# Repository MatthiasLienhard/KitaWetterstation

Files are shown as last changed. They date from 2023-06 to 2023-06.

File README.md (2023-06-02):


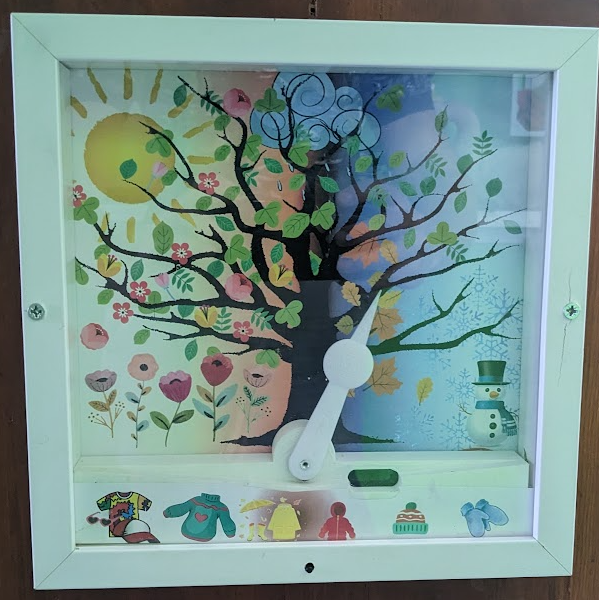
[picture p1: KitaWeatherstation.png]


# KitaWetterstation
Weather station with animations for kindergarden.
This video shows the weather station in action: https://youtu.be/sKCQWrAyeEQ
The 3d model files are also on thingiverse: https://www.thingiverse.com/thing:6057646

# Function
A press on the button wakes the ESP32 from deep sleep. It connects to wifi, and displays an animation with the LEDs and pointer. After wifi is established, the DWD weather API is queried for the current local weather information. This information is evaluated into 5 categories, mainly on temperature and rainfall. The category is displayed with the pointer, and corresponding clothing lights up. The OLED display also shows the weather information with an icon, and the exact temperature. Further it used to display battery state and issues, such as problems with the wifi connection. 
The device is battery operated. The battery is expected to run about 1 week before it needs recharging with a USB charger. 

# Implementation
The project is implemented in micropython, with asyncio to facilitate processing of concurrent tasks. For the first use, I implemented a function save_wifi(ssid, pw) to setup a wifi connection to an access point. This creates a file credentials.txt storing this information. 

# Components
* Ikea Frame SANNAHED 25x25 cm
* 3d printed base to hold the motor and hide the electronics in the frame. 
* Artwork for the background and the clothing items to light up. 
* ESP32 dev board with battery charging circuit and low standby current. I used TTGO T7
* SG90 Hobby servo motor.
* 6 LEDs of a RGB Neopixel stripe 
* I2C oled display 0.92'', 128X32 pixel.
* 1000 mAh lithium ion battery 
* tactile button
* some mosfets to reduce standby current of LEDs and Motor. I used IRLML6344 and SI2305 for a high side switch. Since these are SOT-23 SMD components I used adapter PCBs to integrate them in the circuit.

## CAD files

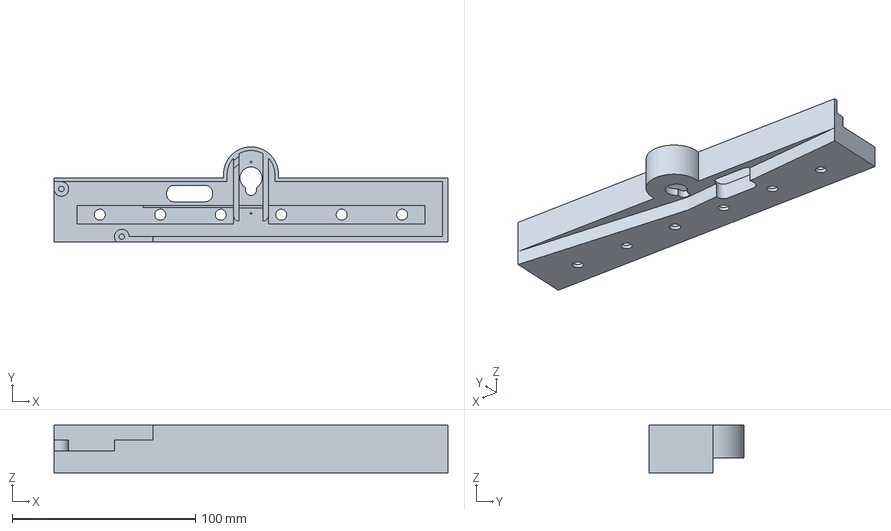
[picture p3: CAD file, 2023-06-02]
3dmodel/kitathermometer-Body.3mf
215.0 x 52.0 x 26.0 mm

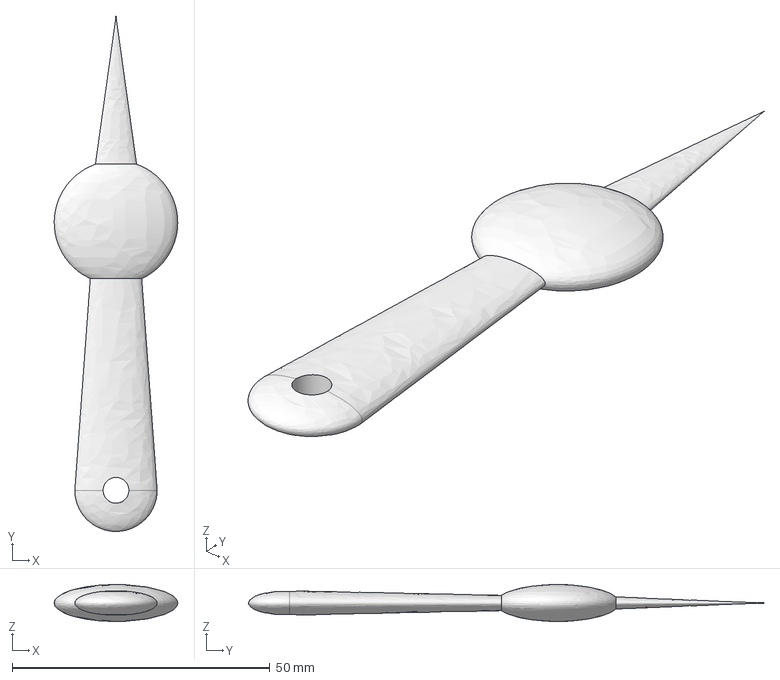
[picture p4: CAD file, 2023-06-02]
3dmodel/zeiger.FCStd
24.0 x 100.0 x 7.19 mm

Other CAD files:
3dmodel/kitathermometer.FCStd
3dmodel/kitathermometer.3mf
3dmodel/zeiger.3mf

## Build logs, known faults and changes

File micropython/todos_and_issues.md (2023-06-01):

todo: webrequest assync
zones:>30: sonnenchreme, <30 t-shirt, <20 pulli, rain: regenjacke, <15: jacke,  <10: Mütze,  <5: Handschuhe

priority: 2<1<3<4<5<6<7
save zone thresholds

save last weather result
only request if d time > 15 minutes

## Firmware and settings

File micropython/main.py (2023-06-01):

# main.py -- put your code here!
from servo import Servo
from display import Display
import neopixel
import time
from machine import deepsleep, Pin, I2C, ADC
import esp32
import utils
from utils import save_wifi as wifi
from utils import save_thresholds

from bitmap import BitMap
import uasyncio as asyncio

# initialization
wakeup_pin = Pin(4, Pin.IN, pull=Pin.PULL_UP,value=1, hold=True)

power_pin = Pin(33, Pin.OUT, value=1)  # activate VBAT
battery_pin = ADC(Pin(35), atten=ADC.ATTN_11DB)
vbat = battery_pin.read_uv()/1000000*2
print('battery voltage: {}V'.format(vbat))
i2c = I2C(0, scl=Pin(22), sda=Pin(21))
display = Display(i2c, 128, 40, False, start_msg=None)
# battery between 3.5 (empty) and 4V (full)
display.battery(80, 10, charge=max(0, min(100, (vbat-3.5)/.5*100)))
display.text('{:.1f}V'.format(vbat),80, 24)
if vbat < 3.5:
    display.show()
    power_pin.value(0)  # VBat inactive
    
    esp32.wake_on_ext0(pin = wakeup_pin, level = esp32.WAKEUP_ALL_LOW)
    time.sleep(3)
    display.poweroff()
    deepsleep()


np = neopixel.NeoPixel(Pin(17), 6)
servo = Servo(pin=Pin(16), pwm_freq=50, min_ms=.4,
              max_ms=2.15, range_degrees=90)


# shutdown 
def shutdown():
    for i in range(len(np)):
        np[i] = 0, 0, 0
    np.write()
    servo.pwm.deinit()
    print('go to sleep...')
    power_pin.value(0)  # inactive
    # _ = wakeup_pin.irq(handler=None, trigger=Pin.IRQ_FALLING,
    #                   wake=DEEPSLEEP)  # configure wakeup
    esp32.wake_on_ext0(pin = wakeup_pin, level = esp32.WAKEUP_ALL_LOW)
    display.poweroff()
    
    deepsleep()
icon_names = [['cloud', 'rainbow', 'snow', 'clear-day'], ['cloudy', 'rain', 'cloudy-wind', 'wind'],
              ['partly-cloudy-day', 'clear-night', 'sleet', 'degree'], ['unknown', 'wifi', 'None', 'None']]
icons_all = BitMap.from_file('weather-icon-set.bmp')
icons = {}

for i in range(4):
    for j in range(4):
        if icon_names[i][j] != 'None':
            icons[icon_names[i][j]] = icons_all.crop(30*j, 30*i, 30, 30)

icons['partly-cloudy-night'] = icons['partly-cloudy-day']
icons['fog'] = icons['cloud']
icons['hail'] = icons['snow']
icons['thunderstorm'] = icons['rain']

numbers_all = BitMap.from_file('numbers.bmp')
numbers = {}
for i in range(10):
    numbers[str(i)] = numbers_all.crop(20*i, 0, 20, 30)
numbers[','] = numbers_all.crop(200, 0, 10, 30)
numbers['.'] = numbers_all.crop(210, 0, 10, 30)
numbers['-'] = numbers_all.crop(220, 0, 15, 30)
del numbers_all


del icons_all
# del icon_names
gc.collect()

# missing icons


display.draw_image(icons['wifi'], 40, 2, invert=True)
display.show()


async def main():
    display_task = asyncio.create_task(display.cycle_images(
        [None, icons['wifi']], 40, 2, invert=True, delay=.2))
    neopixel_task = asyncio.create_task(utils.np_animation(
        np, fun=utils.colorband, steps=30, np_diff=.05, brightness=30))
    # neopixel_task=asyncio.create_task(utils.np_animation(np, fun= utils.kitt,steps=20, back=True, brightness=10))
    servo_task=asyncio.create_task(servo.steps(positions=[0, 1/3, 2/3, 1, 2/3, 1/3, 0,-1/3, -2/3,-1, -2/3, -1/3 ],  sleeptime=1/6))
    connected = False
    connected = await utils.connect_wlan(*utils.read_credentials())
    #await asyncio.sleep(10)
    
    display_task.cancel()
    display.draw_image(icons['wifi'], 40, 2, invert=True)
    if not connected:
        for shift in range(3):
            display.line(39+shift, 2, 69+shift, 32, 1)
            display.line(39+shift, 32, 69+shift, 2, 1)
            display.show()
            
    else:
        #todo: depend on machine.reset_cause() 
        
        #display.fill_rect(0,0,128,32,False)
        display.fill(0)
        display.draw_image( icons['unknown'], 0,2, True)
        display.draw_image( icons['unknown'], 45,2, True)
        display.draw_image( icons['unknown'], 90,2, True)
        #display.text('Messstation',32,24)
        display.show()
        

        wetter = utils.get_weather()
        if wetter['temperature'] is None:
            utils.set_local_time()
            display.fill_rect(0,24,128,8,False)
            display.text('Vorhersage',32,24)
            display.show()
            wetter = utils.get_weather_fc()

        for k, v in wetter.items():
            print('{}: {}'.format(k, v))

        display.fill(0)
        # display.text(['{} and {}'.format(wetter['condition'], wetter['icon']),'{}*C'.format(wetter['temperature'])], valign=1, halign=1)
        # display.draw_image(icons.get(str(wetter.get('icon')), icons['unknown']), 0,2,True)
        print('draw icon')
        display.draw_image(icons.get(str(wetter.get('icon')), icons['unknown']), 0, 0, True)
        offset = 30
        if wetter.get('temperature') is None:
            display.draw_image(icons['unknown'], offset, 2, True)
        else:
            for c in str(wetter['temperature']):
                digit = numbers[c]
                display.draw_image(digit, offset, 2, True)
                offset += digit.width
            display.draw_image(icons['degree'], offset, 2, True)
        rain=wetter.get('precipitation_10', wetter.get('precipitation'))
        if rain:
            msg='{}mm'.format(rain)
            display.fill_rect(0,24,8*len(msg),8,False)
            display.text(msg,0,25)
        display.show()

        temp_range = (5, 25)
        if wetter.get('temperature') is not None and rain is not None:
            servo_task.cancel()
            neopixel_task.cancel()

            zone, lights=utils.get_zone(wetter['temperature'], rain)
            color=utils.heatcolor(wetter['temperature']/30, 50)
            for i in range(6):
                if i in lights:
                    np[i]=color
                else:
                    np[i]=0,0,0
            np.write()
            # servo_pos = ((wetter['temperature']-temp_range[0]) /
            #            (temp_range[1]-temp_range[0])-.5)*2
            servo_pos=(zone-3)/3
            servo_pos = max(min(servo_pos, 1), -1)
            
            servo.set(servo_pos)
    await asyncio.sleep(12)

    neopixel_task.cancel()
    servo_task.cancel()

asyncio.run(main())

# condition: dry┃fog┃rain┃sleet┃snow┃hail┃thunderstorm┃
# icon in clear-day | clear-night | partly-cloudy-day | partly-cloudy-night | cloudy | fog | wind | rain | sleet | snow | hail | thunderstorm




shutdown()

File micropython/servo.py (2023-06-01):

from machine import PWM
import time
import math
import uasyncio as asyncio

class Servo:
    def __init__(self,pin,pwm_freq=50, min_ms=1, max_ms=2, range_degrees=90):
        min_duty=1024*min_ms/(1000/pwm_freq)
        max_duty=1024*max_ms/(1000/pwm_freq)
        self.range_degrees=range_degrees
        self.center=(min_duty+max_duty)/2
        self.dev=(max_duty-min_duty)/2
        self.pwm = PWM(pin,freq=pwm_freq, duty=int(self.center))
        
    def set(self,position=None, degrees=None):
        if position is None:
            position=(degrees / self.range_degrees) * 2 - 1
        if abs(position)>1:
            raise ValueError('deviation of {} exceeds range [-1, 1]'.format(position))
        self.pwm.duty(int(self.center+position*self.dev))
    
    def offset(self, position=None, degrees=None):
        if position is None:
            position=(degrees / self.range_degrees) * 2
        self.set(self.position+position)
        self.center+=self.dev*position

    
    @property
    def position(self):
        return (self.pwm.duty()-self.center)/self.dev
    
    @property
    def degrees(self):
        return (self.position+1)/2*self.range_degrees

    async def goto(self,position=None, degrees=None,timespan=1, sleeptime=.1):
        if position is None:
            position=(degrees / self.range_degrees) * 2 - 1
        start_pos=self.position
        direction=position-start_pos
        timespan*=1000 # in ms
        start_time=time.ticks_ms()
        while True:
            passed=time.ticks_diff(time.ticks_ms(), start_time)
            self.set(start_pos+direction*min(1,passed/timespan))
            if passed>=timespan:
                return
            await asyncio.sleep(sleeptime)
         

    async def steps(self,positions=None, degrees=None,sleeptime=.5):
        if positions is None:
            positions=[d / self.range_degrees * 2 - 1 for d in degrees]
        i=0
        while True:
            if i==len(positions):
                i=0
            self.set(positions[i])
            i+=1
            await asyncio.sleep(sleeptime)

    async def sin(self,pos1=-1, pos2=1, freq=1, sleeptime=.1):
        if pos2<pos1:
            pos1, pos2= pos2, pos1
        ampl=(pos2-pos1)/2
        center=(pos1+pos2)/2
        start_dist_rel=abs((self.position-center)/ampl)
        await self.goto(center, timespan=start_dist_rel/freq, sleeptime=sleeptime)
        start_time=time.ticks_ms()
        while True:
            passed=time.ticks_diff(time.ticks_ms(), start_time)
            x=math.sin(passed/1000*2*math.pi*freq)
            self.set(x*ampl +center)
            await asyncio.sleep(sleeptime)

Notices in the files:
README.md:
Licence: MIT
